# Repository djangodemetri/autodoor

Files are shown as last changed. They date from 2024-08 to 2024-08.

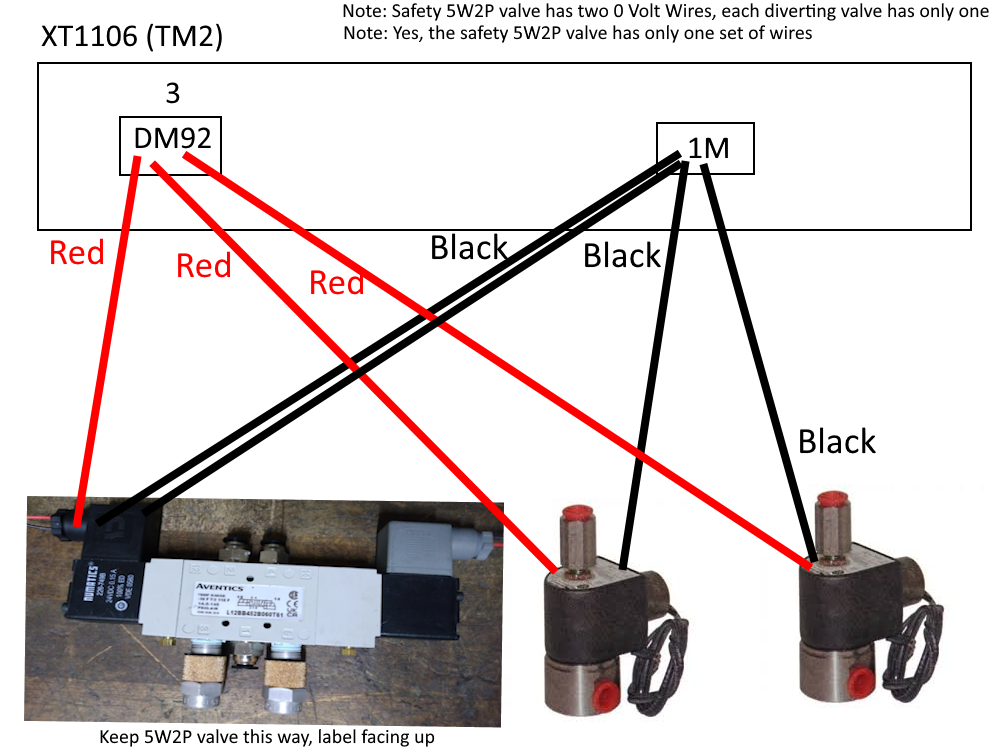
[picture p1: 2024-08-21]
Technician Diagrams/Safety 5W2P Valve_Diverting Valves Wiring Diagram.png

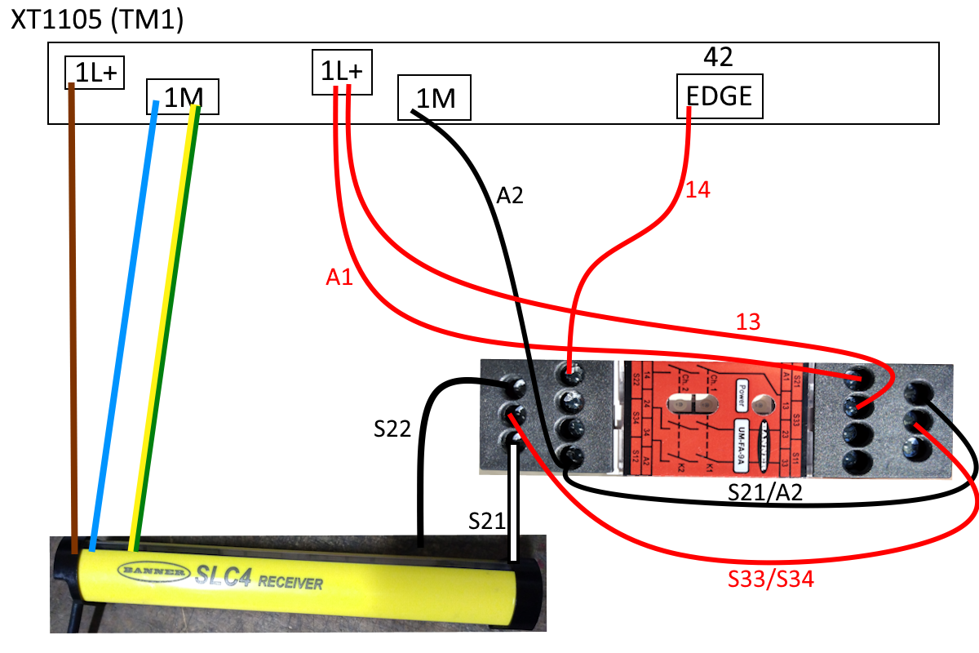
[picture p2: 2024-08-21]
Technician Diagrams/Light Curtain Receiver_Safety Relay Wiring Diagram.png

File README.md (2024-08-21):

White Industries is a machining company for billet aluminum bicycle components located in Petaluma CA. 
In order to meet growing demand, they hired me to create a pneumatic auto door that could be mounted to all of their machines (routers and lathes).
The company did not have any engineers as employees so I was the engineer and manager of the project.
In 2.5 months I designed, built, and tested a fully functional autodoor that meet all the necessary requirements:
1 Controlled by the host machine through ladder code
2 Scalable 
3 Safety (by using a Banner light curtain)
4 Documented so that the other employees could troubleshoot, maintain, and adapt the autodoor to other machines.
Please see the video demonstration for the final product.

It was abundantly fun and I am very thankful for the opportunity.

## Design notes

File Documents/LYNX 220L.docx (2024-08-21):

Continue:

Return switch valves

Return DIN connectors

Return Through beam

Return air cylinder brackets

Return M12 connector (wait) (Also determine color code before reutnring the M12 connectors

Call Bimba for adjusting air cushion

Emitter needs to have a U bracket that wraps around the back. The mounting plate is either above or below the plane of the emitter. Mount it to the two left screws only. We need to print washers. We need to find the distance of the emitter so the angle is okay, it might already be that 8cm but double check.

We need to find exact dimensions of the nose thread. Then we need to use the manual

We need to work in adjustability. For the air cylinder mounting we would want to drill slots instead of holes so that the air cylinder can be rotated if need be.
Make mounts relatively simple to machine, boxy

Interfacing:

The through beams must not open the door when it’s closed, aka, when DIC.M is triggered.

Through beam relay may not be necessary but it does isolate the sensors from a large power draw.

Why are there so many conditions for CLINT? Possibly it should be rewritten?

SSTA might be redundant because it’s included in the open door code? Or should it be in the close door code?
Maybe INRST should be wired to a button on the console, R17.6 which is the auto door button. If we want to be extra safe we could create another branch with CLINT and then a custom button/bit, but that wouldn’t work because it’s OR logic. We should replace INRST with R17.6 , because we can’t affect any other logic that may have INRST, but we have to make sure INRST did not provide any additional safety. *We don’t need to do this because KADOP will keep the door open and once CLINT is unlatched, the situation will return to normalcy.

Do we want the secondary solenoid to be wired normally open the door or normally close the door? If the power goes out nothing happens

Write OR condition for the secondary solenoid to be triggered, don’t purely rely on light curtain to trigger it

Think how software will interact with EDM. So the cycle is that the light curtain gets triggered, the safety relay is tripped, but because of the software, the XT1104 relay is held. With the EDM the light curtain may try to return to normal but it can’t because the reset circuit is being held open by the XT1104 relay, indirectly of course. The user hits the button and M53 executed, now the XT1104 input is off, the light curtain that is only held back by the reset circuit is now running again and everything returns to normal.

Be careful about adding DIC.M or DOC.M to reset code because this is what would define if the door could be closed before or after it has triggered DOC.M.

CLINT triggers DOP.R which then triggers KADOP, so once CLINT is off which should return to the normal state.

The operator closes the door by using M53 then the door is triggered. We need to make sure the machine does not start running the M program. It is probably safe to assume that DIC.M is already written and prevents the M program from running, considering they have just left DIC.M normally closed, implying that it would not run the code otherwise.

Problems:

ARST connects to INRST, what is ARST?

DOP.R/DOC.R have all the code written for them already. Does it make more sense to write both solenoids to DOP.R/DOC.R and have the switch valves run off the XT1104 input or does it make more sense to just connector DOP.R/DOC.R to the XT1104 input through the software? Let’s connect them through code. Figure out:

How does it reach return state?

Does this inhibit the system overall?

Delay implementing the force guided contacts. They are easy to retrofit and are not crucial quite yet. Plus it’s cheap so it’s easy to convince him later after the sting of the light curtain.

Does SDOC need to exist? By the time the door is ready to be closed, the primary code is now being executed. In fact, maybe it makes sense to not even allow the secondary solenoid to close the door.

ARST and INRST are controlled by the ALARM RESET EMG. RELEASE button

Grounding Forum (https://diysolarforum.com/threads/why-do-dc-systems-not-make-use-of-grounding-to-the-same-extent-as-with-ac.5152/)

dc Knowledge (https://electronics.stackexchange.com/questions/417172/why-do-engineers-usually-short-ground-and-negative-ports-on-a-dc-power-supply)

Wire neutral and earth together but only per unit, so we’ll have three separate wire bundles for the solenoid valves.

Is the normal output of the safety relay high? *Assume it’s high because it has and switches

Ground bolt is 7.5mm Looks like #10 (https://www.google.com/search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)

Code walkthrough:
1 Door closing, door not opening, light curtain triggered aka goes low, door not closed, ?

2 CLINT is latched because of ARST

3 DOP.R is latched by CLINT

4 *CLINT is opened by light curtain not triggered but DOP.R still on because KADOP/secondary system disabled because SDOP controlled completely by CLINT

5 *M53 is executed which turns off DOC.R on the open code and on close code and triggers DOC.R to close the door

Mounting:

Main solenoid: 27cm

Air cylinder: 66.35cm

Screw arrangement: 34cmx25cm

U brackets: 8/32in

5W2P brackets: M3

Diverting valve brackets: Probably SAE of M5

Installation Problems:

Switch valve does not function as intended

This depends on the switch valve, double check DIN connector fits and then order another

Return switch valves

Relay has slow return time (might not matter)

Second conveyor sensor did not come in d

One more relay for secondary solenoid (might not matter)

Adjust cushions

Potential Revisions:

Order equipment from a source other than McMaster, (likeG&G Hydraulics) to save cost. These companies have longer shipping time and less customer service but lower prices in lieu.
Likely the intake flow control valve and exhaust flow control valve are redundant. The exhaust flow control valve is more expensive so if metering is possible with only the intake flow control valve, likely $107 could be saved. If exhaust flow control valve is indeed skipped remember to buy mufflers for the main solenoids’ exhaust ports, 4 mufflers for 4 exhaust ports.

SMC’s sine air cylinder will naturally slow the cylinder the last couple inches or so due to its built in design. It’s as much as the 6258K154 (https://www.mcmaster.com/6258K154/) but has a 6-8 week lead time. Should be installed similarly to the 6258K154 but that has not been confirmed.

An air cylinder that has only cushions but not a magnet inside the cylinder for sensors to detect, (called sensor ready), is half the price; for example, 6475K216 (https://www.mcmaster.com/6475K216/) (double check specs before ordering). Mount a magnet on the extending end of the piston, (so the proximity sensor would be mounted at the position where the piston is fully extended).

If multiple machines will be fed from the same supply line then buy one regulator and supply line solenoid valve. Assuming the machines would be operable on the same pressure which should be reasonable unless one of the machine’s strokes is far longer than 24in.

Facts:

M52 open door

M53 close door

Supply pressure: 120psi

Outlet voltage:

232 data interface

0iD or 32iA

Door travel: 21 2/16 inch (53.657cm)

[

101533-00738

101533-00739

101533-01005

]

Door Height: APPROXIMATELY 44.5 inches

When one side is being pressurized, the other side will be evacuated

Serial Number: ML0022-006463

M02 is end of program code that might unlock the interlock

User Who Offered Help (https://www.practicalmachinist.com/forum/threads/robotics-automation-engineer.404319/)

Tips (https://automationforum.co/thumb-rules-and-tips-for-control-valves-selection-and-sizing/)

Adapters are 9/16

Exhausts are 11/16

Considerations:

We could use the code already in place or use external commands (M9-).

The door needs to be openable if the power goes out

For the manual air control valve it must depressurize more than the main control valve does.

https://www.machinetoolproducts.com/versabuilt-robotics-versadoor-pneumatic-cnc-door-opener-for-automation

*The door appears to not lock at all

*If the door is open, nothing else will happen because of that lock sensor

Might consider waiting to buy the safety beam until we see the door speed(a0)

The sensor only knows when the door is not closed. The operator will push the button to start the code.

M53 may already hop to next line of code. It may not know to wait because manually operated, it never needed to know

This auto door will clearly interface with the CNC, maybe it’s faster to just building the auto door and plug it in; don’t mount it and just watch the logic happen in real time. This rides on the assumption that we can easily make the adjustments. Maybe one exception would be depending if the safety relay will hold logic.

Does every piece have female or male threads?

For the 24inch stroke cylinder we could install more bump stops

References:

Midaco:

800 994 0146 Darrell

DN Solutions (Previously Doosan and Daewood):

888 dns 0010

973 618 2500

Fanuc US:

888 fanuc-us

Airflow Calculations:

At 60PSI the airflow is 8SCFM which (https://www.coastpneumatics.com/scfm-conversion/) is 1.62CFM at T=72 P=74.4PSIA PB=14.7PSI H=.85. The Cv is calculated to be .4 (https://www.swagelok.com/en/toolbox/cv-calculator).

General Parts:

Tubing

Piston Mounting Brackets Stationary

Piston

Piston Mounting Brackets Kinetic

Pressure Regulator

Solenoid

Control Valves Open (maybe needle valve?)

Control Valves Close (maybe needle valve?)

Piston lubricant

Release Value for safety stop

Main Solenoid:

4 to 2 solenoid

4xt33, 4ka92

How does it respond to logic?

Are the exhaust vents threaded? Yes because they say female outlets

Would cylinder speed depend on both pressure and depressure rate? This may be fixed if we have valves already, the valves needed to block the exhaust ports.

Consider flow rate: is 9 CFM enough?

https://www.grainger.com/product/ARO-Solenoid-Air-Control-Valve-2G621

Make sure it can operate at the PSI we are actually using

The supply will never be feeding both the solenoids at once so we only need to consider CFM for one solenoid.

Can we complete cut off solenoids if they’re only 4 way? *Because they get completely isolated thai shouldn’t be a problem. *So we shouldn’t need switch valves for the exhaust ports.

If 9CFM is too high, consider a lower CFM solenoid if cheaper?

https://www.amazon.com/ARO-Ingersoll-M212SS-024-D-G-2-Position-Solenoid/dp/B06XFMM7LT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

*200mA

Cheaper model with 50 min (https://www.zoro.com/aro-solenoid-air-control-valve-14-in-24vdc-a212sd-024-d/i/G2774816/?gclsrc=aw.ds)

7/6 Addendum:

Since the cushioning does not behave the expected way and we need to use exhaust ports we will likely need to control the speeds independently with 5/2 solenoid valve.

https://www.mcmaster.com/6425K14-6425K143/ This requires four less DIN(-$42), 4 exhaust control valves with muffler (+$24.16)[minus silencers], potentially both flow control valve. Would we want meter in only for flow valves?if we have to valves metering out then we might restrict the depressurize system too much. Difference in threads may need attention later, but because NPT male to NPTF female it may not deform those threads and it should be okay.

Tubing:

Fittings are usually push to connect

Make sure it can operate at the PSI we are actually using. It can, according to website linked right below.

Make sure the CFM is enough

Max SCFM at 60PSI is 3.5 (https://www.greenlinehose.com/content/Hose%20Flow%20&%20Sizing.pdf)SCFM

Mounting:

https://www.modularcomponents.com.au/building-blocks/

Angle Mount Information (https://cdn.automationdirect.com/static/specs/nitrad2hd2bore.pdf)

Angle Brackets for Air Cylinder (https://www.automationdirect.com/adc/shopping/catalog/pneumatic_components/pneumatic_air_cylinders/air_cylinder_accessories/d2am-1)

Pistons:

https://www.automationdirect.com/adc/shopping/catalog/pneumatic_components/pneumatic_air_cylinders/iso_15552/g40m500md-mc

https://www.hydraulicmegastore.com/product/32-550amak/

https://www.zoro.com/speedaire-air-cylinder-1-12-in-bore-22-in-stroke-nfpa-double-acting-5teg5/i/G7647272/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

https://www.mcmaster.com/6258K149/

Half of the price can be saved if we create a custom sensor setup or cushion setup. It’s possible to mount a magnet on the end of the piston, (where it mounts to the door), and then just have the proximity sensor at the middle point, (wherever the mount lies when the cylinder is fully retracted).

We have three states but only two inputs, but the normal force must equalize the piston force so you only need two inputs.

Calculator Cylinder Size (https://www.automationdirect.com/pneumatics/cylinders/cylinder_sizing)

Operation force is 15 pounds, 18.75 with 25% safety which is a minimum. We can assume there won’t be too much loss since the system doesn’t have that many components. MAKE SURE ROD DIAMETER MATCHES TABLE

RETRACTING FORCE WILL BE LESS

Air Cylinder Factors:

Bore

Pressure

Action

Damping

Safety

Airflow Calculations:

Assume maximum case.

Assume that pressure regulator is very close to the solenoid. Meaning the only piping where CFM becomes necessary is primary solenoid to cylinder.

Assume inner diameter of air housing is the same as the outer diameter.

Airflow Calculations (https://www.youtube.com/watch?v=Fbw3QlP2hTM)
Cylinder Dimensions:

Bore Diameter=29.633mm

Rod Diameter=7.874mm

Stroke=558.800mm

Pressure=60psi=.414MPa

Piping Dimensions:

Length=2000mm

Diameter=3.175mm

Airflow=2.435 cfm (23cfm from other calculator)

Sine cylinder has slowing effect naturally.

Seems like the REC cylinders are all legacy, why is that? (RECB25-550)

Is the slowing controlled by PLC or is it just mechanical?

Adjustable slowing?

If we order a cylinder without the reed switch does it still come with a magnetic inside?

Anything special about setting it up compared to other cylinders?

Returns?

Auto switch?

Force chart?

https://www.smcpneumatics.com/RECL25-550-C80C.html

Pneumatic Cylinder Sensor:

DOC.M is named “Auto Door Open Check Sensor.” NO sensor, when sensor is triggered then the NC DOC.M is triggered and the machine knows the door is already open.

Regulator:

Consider that the nominal pressure may differ, maybe buy a slightly higher PSI gauge

Make sure the pressure adjustment range has a range to and around 60PSI (Likely we would want to go lower than 60PSI, not necessarily higher so that sacrifice can be made if needed, but try not to)

Make sure CFM is enough

Filter

Bowl for condensation?

Light Curtain:

To back off the cylinder, it’s simple just triggering it backwards using the same system. Except when the power goes out this will not be viable for safety or just to open it. THIS WILL DEPEND ON WHAT SETUP THE AIR CYLINDERS WILL BE LIKE, maybe needle out system?

The door handle is going to trigger the light curtain unless we mount it at least 3.5 inches from the door’s edge.

Normal state is 24V, hazard detected is 0V (open door is 0V)

Does the signal stay low until the person’s hand is removed or is it on a timer?

Edge to handle: 4 inches

Edge to handle with arm: 6 inches

SEE CONSIDERATION(a0)

Door must wait until okay signal is given, (this likely could be the same as the normal close door and continue procedure). Check if there is a timer or if it’ll stay open indefinitely.

Fingers must be able to be unclamped?

How many pounds to open the door? Could an operator open it manually, in the case the power goes out?

Alternative: Have it closed with a button and require that someone is holding the button to close the door. This may eliminate the need for a safety beam

https://www.pepperl-fuchs.com/usa/en/classid_83.htm?view=productdetails&prodid=67155#datasheetcontent

If OSSD is used then a safety relay is needed as well. Make sure it is not a pulse signal model?

Consider a IP54 box (https://www.sick.com/media/docs/1/01/101/Operating_instructions_ReLy_OSSD1_en_IM0076101.PDF)

*It looks like the safety sensor only holds voltage when the object is obstructing the beams aka pulse.

We could remount the handle. Because it won’t be used much anymore it doesn’t matter if it’s in a weird or inconvenient spot.

https://www.wolfautomation.com/light-curtain-ultra-thin-thru-beam-160mm-det-1/

Does the light curtain run on AC or DC? DC
In safety, if the light curtain is exposed to coolant or water or any other substance inspect before using it again.

General Informaiton (https://info.bannerengineering.com/cs/groups/public/documents/literature/122452.pdf)

Trip or latch (Maybe buy a light curtain that does both and we can troubleshoot in the moment). Maybe just skip because safety relay may not be compatible.

Does the safety relay have enough power to operate the directional valves? Doesn’t matter if we use trip system.

https://www.bannerengineering.com/us/en/products/part.805795.html $642

https://www.bannerengineering.com/us/en/products/machine-safety/safety-modules/sr-im-series.html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

Through Beam Addendum:

https://www.wolfautomation.com/photoelectric-sensor-through-beam-pnp-45595/

https://www.balluff.com/en-us/products/BOS02AW

Throw dust into beam’s path to test if it still works

Says (https://www.automationdirect.com/adc/shopping/catalog/sensors_-z-_encoders/photoelectric_sensors/general_purpose_photoelectric_sensors/qmrhd-0p-0a)to use 24AWG, 100mA max which my calculations give 2.4W

Visible light may be susceptible to other light

Back to Light Curtain Addendum:

Is it possible to have the light curtain wire directly to the Lynx? It would have to compensate for the time difference between outputs to know when it’s a real trip. It would also need to input relays, which is not a bad thing considering there are plenty of spares.

Page 19 for Table of Terminals (https://media.distributordatasolutions.com/allenbradley/2017q1/74da9d8dcf82595eb507972877c303329b069640.pdf) Diagram (https://literature.rockwellautomation.com/idc/groups/literature/documents/at/safety-at065_-en-p.pdf)

EDM Explanation (https://blackcontrols.com/blog/f/external-device-monitoring)

Page 55 for Force Guided Upgrade (https://info.bannerengineering.com/cs/groups/public/documents/literature/179480.pdf) Possibly just across the safety system

Arc suppressors, see datasheet linked on page 60, Page 8 (https://info.bannerengineering.com/cs/groups/public/documents/literature/141249.pdf) suggests that we do not need arc suppressors because we are operating under 151V.

Prove the IM-T-9A can be used

Force Guided Relay (https://www.wolfautomation.com/relay-force-guided-3no-3nc-24vdc-led/)

With respect to choosing polarity for EDM reset circuit, it must be NC because the contacts are mechanically linked, so you can’t have 5 pin.

EDM protects against returning to normal state from safety state, but what if the contacts are welded in normal state and cannot be triggered to safety state?

1brown 2white 3blue 4black 5green

Directional Control Valve:

Do we need one that exhausts the air? Yes, because that is the third connection

Do we want spring return? Yes, it’s cheaper and should work just fine in this situation.

NC or NO? It appears we can set it up whichever way. The only possible problem is that hooking it up “backwards” must have airflow problems depending on how the solenoid is created.

There is a switch valve with speed control but it only has 1/4inch ports. Will there be enough adjustment to slow the air enough? Physically look at 1/4inch compared to 1/8inch, would the CFM change that (https://www.greenlinehose.com/content/Hose%20Flow%20&%20Sizing.pdf) much (https://www.engineeringtoolbox.com/air-discharge-hose-d_1523.html)? Will it actually save cost if we have to order different size hoses and connectors? Also is the speed electrically controlled? Don’t need it

Is 6ms fast enough? If so, no need for fast-switching. Don’t need it

https://www.automationdirect.com/adc/shopping/catalog/pneumatic_components/directional_control_solenoid_valves/solenoid_valves/avs-3111-24d

General Directional Valves (https://www.mcmaster.com/products/pneumatic-switches/single-action-electrically-operated-air-directional-control-valves-11/)

Predicted airflow is 3.36SCFM

*125mA

Revision:

https://www.emerson.com/en-us/catalog/automation-solutions/fluid-control-pneumatics/general-service-valves/asco-320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

https://store.flw.com/products/asco-series-8320-3-way-solenoid-valve-8320g174-24-dc.html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

Shuttle valve is a candidate but it works on pressure differential which mean we would need to have one of the solenoid operating at a higher pressure.

Use a 4 way 2 position valve with the exhaust valve sealed

Two 2 way valves that are wired in opposition

Different Spool Valves (https://www.sunhydraulics.com/sites/default/files/media_library/tech_resources/TT_US_PODirectional_Aug2015.pdf)

https://www.electricsolenoidvalves.com/1-4-3-way-24v-dc-electric-solenoid-valve/

https://us.misumi-ec.com/vona2/detail/221300030450/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

Probably L-Port type valve

For Parker manual (https://www.parker.com/content/dam/Parker-com/Literature/Fluid-Control-Division/Bulletins/PDFs/Parker-General-Cat-3-Way-Valves.pdf), page 17-B7

Search for “l-port” and “3 way selector”

Top choice for now (https://www.mcmaster.com/2565N15/)

B30

Alternative for the future (https://tameson.com/products/tp-db014b040f-024dc-solenoid-valve-3-2-way-1-4-inch-brass-fkm-0-2bar-24vdc)

Air-Exhaust Control Valve:

We might not need this at all, depending exactly on how the two solenoids interact

Supply Solenoid:

Use two relays, normally open in parallel with and logic to control the supply solenoid. The and logic is to have redundancy in the system. (Probably skip this, it doesn’t seem to add any more safety)

Make sure it can operate at the PSI we are actually using

Make sure CFM is good. With a Cv=1.4 the allowed airflow is 27 (https://www.swagelok.com/en/toolbox/cv-calculator)SCFM, should be good. But it shouldn’t matter because it’s been fed from the supply and has 1/4inch hosing so its airflow should be the least restrictive of all the components.

Should it be 220V or 24V? 220V limits the options.

Pressure assisted or zero pressure? Zero pressure to be safe
https://www.mcmaster.com/products/on%2Foff-valves/valve-type~solenoid/solenoid-on-off-valves-10/valve-starting-position~normally-closed/pipe-size~1-4/voltage~24v-dc/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

500mA

Flow Control Valves:

Mount as close to the air cylinder as possible for best results, (according to McMaster (https://www.mcmaster.com/products/flow-control-valves/inline-air-flow-control-valves/for-outlet-tube-od~1-8/))

https://www.mcmaster.com/62005k35/

Make sure CFM is good. 4SCFM at 73PSI seems sufficient considering the maximum airflow for hose is 3.5CFM. Should not be very restrictive at 60PSI.

Power Supply:

Does Lynx have power leads?

Must be able to supply:

Supply solenoid

Light curtain

Safety relay

Directional valves

Secondary solenoid

Odds and Ends:

1 to2 -> supply solenoid to primary/secondary solenoid

*Primary solenoid exhaust flow control valve (2 if 5 way solenoid)

*Secondary solenoid exhaust flow control valve (2 if 5 way solenoid)

Teflon tape for sealing connections

1/8inch pressure gauge (pressure regulator, also maybe for testing)

Push-to-connect adapters

Anti-rust spray for drilled holes (must not react with coolant)

Fuses, rated for 32V so we should be okay

2 Relays, through beam sensors, 24V, 100mA, 24AWG compatible

A 24V tester to activate relays (could go without but CNC has huge power draw)

DIN connectors? (https://www.amazon.com/43650-Solenoid-Prong-Connector-Indicator/dp/B09SHKJ7F3?sp_csd=d2lkZ2V0TmFtZT1zcF9hdGY)*Only 2 needed for main solenoid

Probably don’t need any ground equipment since we’re wiring everything through the Lynx

Wire sleeves

https://www.grainger.com/product/SCHNEIDER-ELECTRIC-Slim-Interface-Relay-6-A-Current-6LVJ8

End of Stroke Control:

Release valve controlled by proximity sensor

Progressive spring

Pulse air valve

Add extension to shorter stroke sine cylinder

Just have return stroke slower

Basic Ladder:

They are all push and hold by default

The second relay can be NC, which would be on. But if the relay before it is not on, then it doesn’t have any effect. Even if it is on

Think of toggling buttons as just paying attention to the rising edge

1 The PLC will record all inputs 2 The program will execute 3 the outputs are collected 4

When the tutorial said it was proper to use NO, the physical wiring is normally closed so that when it breaks it’ll open the circuit and turn the output off.

Scan Examples (https://accautomation.ca/understanding-the-plc-program-scan/)

If CLINT goes high then the door opens no matter what. In order for CLINT to go high:

AD Close Relay = 1

AD Open Relay = 0

Safety Sensor Edge On = 0

The door sensor must be out [DCLOSE is DIC.M is door lock sensor (out =0, in = 1)]

KEDGE = 1

Just delete KEDGE and replace it. Deleting KEDGE from CLINT (probably?) won’t affect anything else. Then you don’t have to worry about overwriting anything.

Strategy:

We were looking to buy an auto door option, what would we need to know about setting it up?

1 bill of materials

2 prototyping

3 Clear up details

4 testing

Routine:

Part is done and operator opens the door

User presses foot pedal to release clamp

User cleans part

User replaces part and presses pedal again

Closes the door

User presses button to start program

6/16:

Contact Doosan:
Questions;

Is it 0V that opens the door and 24V that closes it? Does it pulse or does it hold the voltage?

Does M52:

Stop the machine from running?

Does M52 know when the door is fully open?

It waits until the the auto door close/open button is pressed?

Is there a wait on input code?

Would Doosan send us the ladder code?

Considerations:

The sensor only knows when the door is not closed. The operator will push the button to start the code.

M53 may already hop to next line of code. It may not know to wait because manually operated, it never needed to know

If M00 or M01 is executed, then nothing will happen until Cycle Start is pressed.

M53 may already hop to next line of code. It may not know to wait because manually operated, it never needed to know

Cycle:

start:

The program ends. The door opens because of the M52 code.

Once the M52 code is triggered, the voltage on the relay changes, (but is it high or low?).

The machine must know somehow when the door is fully open. (it’s possible to just put this on a timer)

Then the door must wait for some signal from the operator, likely use a button on the console to close it.

Then the operator presses the continue button

The program runs

GOTO start

Interfacing the solenoid with the CNC relays:

The solenoid only accepts either 1 or 0, there’s no idle position.

1. We could only use 104.1 (M52) and once that goes high, then the door retracts. But we have no idea how it behaves in the software.

2. (This is all assuming the code runs either or, not pulse). We could place two relays after the internal relay, one NC and one NO. Then both relays would be in agreement and they would behave like one relay. Then connect them to the ignition terminal on the solenoid. *This would preserve the code’s behavior.

3. We could also use an entirely different single relay that would behave exactly as wanted but we would have to write some code for it, hopefully not much.

If we already have code written for M52 then we could just use M52 in the program.

Solenoid relay hooks into CB104.1 and CB104.2. (Because there are two separate relays that suggests a different logic scheme, one where we would need

Y01.1 is open door (maybe called FRDOP because he said it’s not the direct way). CB104.1 is the I/O name

Y01.2 is close door (maybe called FRDCL because he said it’s not the direct way). CB104.2 is the I/O name

Both M52 and M53 appear to be normally open. But if we fish through the code to see the direct connection we might find differing information

Consider cobot compatibility. But ultimately the cobot could just use a single binary signal as well, essentially the same as the CNC machine.

The hold logic is defined by ladder

Why are there two relays for it? Y1.1, hold until y1.2, unless maintenance and interlock are activated. The interlock requires a set time to elapse before M52 can be executed, which is dictated by ladder code.

Does the kit come with a sensor that tells us when the door is fully open or close?

Phone Call:

Maintanence Mode is M250

Keep relay holds whatever state it was, in case of power off

L000 is “0V”, I think he said it was for AC

Logic high is the M52 command

Address:

1325 Ross St # A, Petaluma, CA 94954

Dump:

Ladder system:

https://www.youtube.com/watch?v=OmqC7_2Ugd8

http://dermako.com/Fanuc_Web_Manuals/Prog/61863ev2.pdf

http://www.cncmanuals.com/fanuc/172/pmc-ladder-language-programming-manual/page/128

https://cdn.automationdirect.com/static/eBooks/PLC%20Handbook.pdf

Toggle Bit (https://www.youtube.com/watch?v=ig5QXp2Bb1s)

Kmap (keep in mind this kmap does not cover every scenario, it excludes the needed and gate)

LC | Auto | OpCl | Scenario: (1=door open || 0=door close)
0 | 1 | 0 | X
0 | 1 | 1 | X
0 | 0 | 0 | 0
0 | 0 | 1 | 1
1 | 1 | 0 | 1
1 | 1 | 1 | 1
1 | 0 | 0 | 1
1 | 0 | 1 | 1

Relay Chain:

Normal function:

Connect internal relay leads to solenoid leads. *When close door, logic high. *When open door, logic low.

Lever:

3 or 4 position

Two NO, one NC

Maintain

Logic to Relays (http://www.relaiscomputer.nl/index.php/elements)

3 Position NC NO (https://cdn.automationdirect.com/static/specs/cents22mmselect.pdf) (https://www.automationdirect.com/adc/search/search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)

Is the safety supplied?

1 Allow the door to operate normally (aka standby)

2 Open the door

3 Close the door

4 Override the primary solenoid

We could have two release valves on when secondary is triggered, which would get rid of any primary influence.

Idle:
Step 1:

a) Trigger both release valves, making primary solenoid completely ineffective no matter which state it is in
b) Activate control relay for secondary solenoid

Step 2:

Secondary Control (Safety):

Return time would be covered because the code will not proceed until the door is fully closed.

Primary is pressurizing left, venting right. Secondary in pressurizing right, venting left. They must have valves because if they’re trying to do opposite actions, then both sides of the cylinder will be vented. The valves should then render one solenoid ineffective.

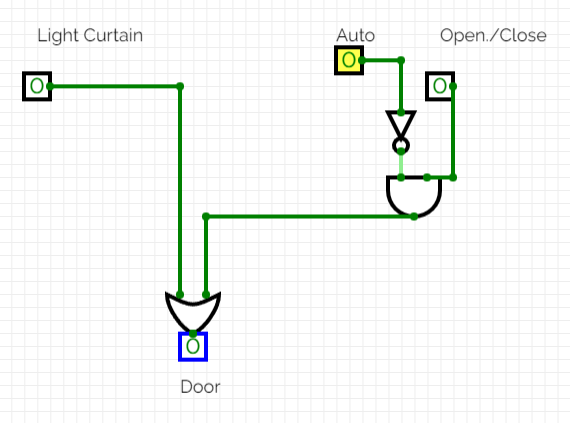
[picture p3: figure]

Caption: If you’re looking at this in the future, I believe the logic is reversed. That is, 0 is open and 1 is close.

4952K721

Do More Designer: vmlcvrgulkerpkbrim@bbitf.com

Temporary:

Primary Solenoid Considerations:

Do we need door close relay? DOC.R

Secondary Solenoid Considerations:
Safety relay is pulse so:

1 Add a few simple lines of code

2 Redo system (This will likely just be Option 1 weirdly)

Let’s go with 1

1 We need code for directional valves

2 We need code for secondary solenoid

So the safety relay goes high temporarily. It will send that pulse to (EDGE.M or KEDGE). The code will run as intended for everything else. Meanwhile:

1 EDGE will trigger Y37.7 which will activate the directional valves. It will need to be toggle code that is turned off likely when DOP.R is.

2 EDGE will trigger Y37.8 which will activate the secondary solenoid. It will need to be toggle code that is turned off likely when DOP.R is.

Because we are able to program toggle bits our system should work.

Software has what we need, even safety and cobot code
The system we made does not directly work with the code but we can easily adapt it. I will need to add a couple lines of code but they don’t change existing code at all. We will back up the data and I have low risk ways of testing the code.

I know how the code roughly will work but not exactly. It makes more sense to figure that side out when we actually have the door built.
So now I’m generating the bill of materials.

Choose which air cylinder

Light curtain placement, remounting the handle?

Trip or latch, meaning bypass software or don’t
Do you want every connection to have push-to-connect?

For less important components would you like to buy them from Amazon or something like that?

Do we want to power the solenoids and light curtain on the Lynx or have a dedicated power supply? Do we know if the Lynx has 24V power source?

Adjustments: 1.5inch air cylinder

Two (or more) safety beams connected in parallel with relays

Airflow Calculations 1/8inch:

1/8in pipe has a maximum airflow of 3.5SCFM. The airflow of the cylinder is _.

Start with finding the airflow of the air cylinder in SCFM and CFM. Use the equation and cross reference it to the table that was given. Once that number is found then it’s a matter of finding pieces that correspond.
Set up assumptions first
A=.110SCFM which makes sense because the total volume of air per minute is only .027CF. We are using a small cylinder, with not many cycles so it makes sense it would be a number pretty close to the volume.

The maximum flow of a 1/8inch hose at around 60PSI is 3.5SCFM which is .88CFM (assuming T=72 P=59.7 B=14.7 H=.84). The calculated airflow for the air cylinder is .1104SCFM, using same parameters listed before.

Cv calculated (https://www.swagelok.com/en/toolbox/cv-calculator) with PI=59.7 P2=54.7 AF=3.5SCFM T=72 SG=1, Cv=.218. All pieces need at least 3.5SCFM or Cv=.218.

Resolution needs to be an inch. Let’s say we have 4in of protection, we need 5 receivers. The receivers normally normally on so that when one faults/power goes out, the door automatically opens. If we connect all 5 in parallel, then it becomes a 5 input and gate. To work with this we could:

1 Wire the sensors in series so that the voltages add up, but that would mean voltage regulation which would be somewhat complicated.

2 Wire the sensors normally off and when one is triggered it gives the 24V for the relay to switch on. This is not particularly safe because if we get an open circuit, (either naturally or from a fuse blowing), the door will continue to operate normally. We could use a relay to reverse the logic. But if one of the sensor fails, (unless short circuit), then the system would have no way of knowing and would continue indifferently.

3 Use 5 different relays all wired correctly. If power cuts out or there is an open circuit, the door automatically opens.

So we make a redundant receiver for each of the “main” receivers, (exception of one), which would cost $300 for the whole setup.

Piston definitely creates too much force to be innocuous

Returns:

3 way 2 position valve from Grainger: branch 742 (5760 commerce boulevard, rohnert park ca 94928)

13 and 14 is an unpowered relay. The CNC relays can either be powered or unpowered.

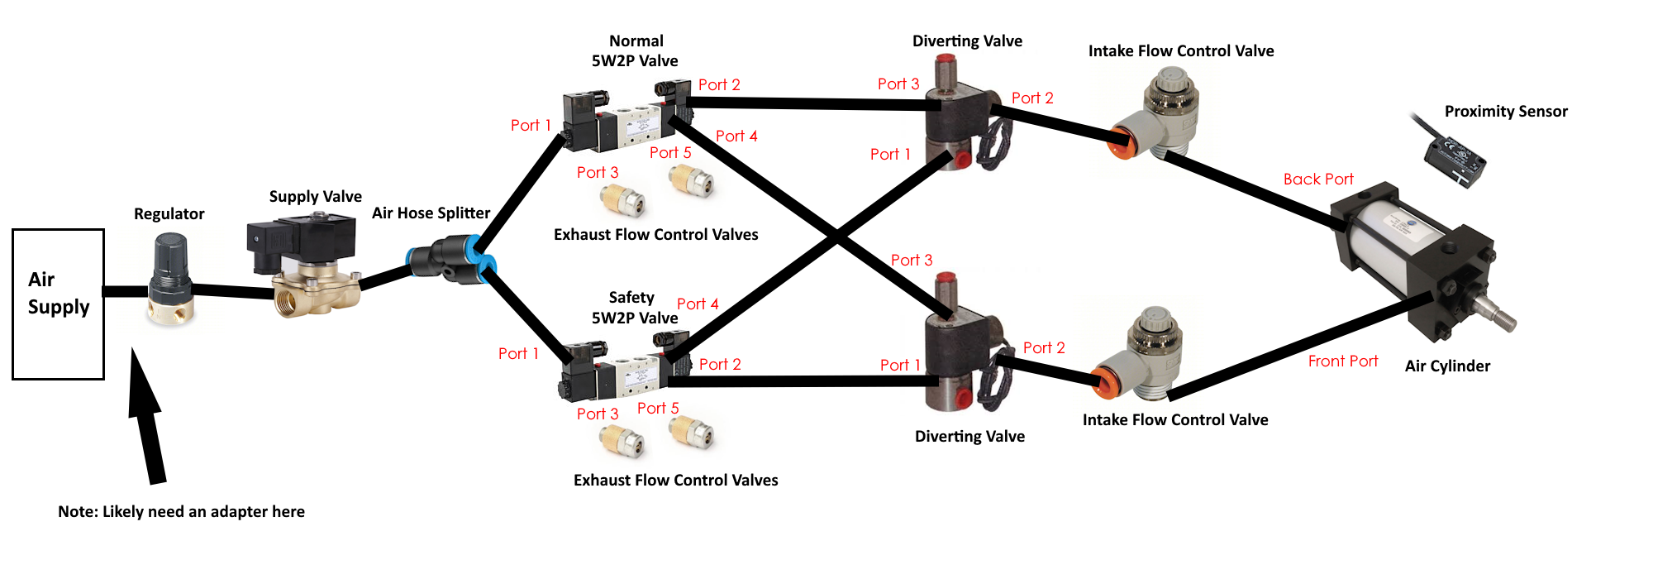
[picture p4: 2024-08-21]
Technician Diagrams/Pneumatic System Layout Picture (Figure _).png

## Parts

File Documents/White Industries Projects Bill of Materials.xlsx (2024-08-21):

Auto Door Project: |  |  |  |  |  |  | Additional Information:
Product | Quantity | Price | Notes | Backup | Company | Order Numbers
Air Cylinder (https://www.mcmaster.com/6258K154/) | 1 | 444.74 |  | 20 inch alternative (https://www.mcmaster.com/6258K144/) | McMaster | In Alec's email | Account email: alec@whiteind.com
Supply Valve (On/Off Valve) (https://www.mcmaster.com/4711K512/) | 1 | 123.78 |  |  |  |  | Account Password: fhAG65!@bm42hk (This may have been changed by Doug)
5 Way 2 Position Valve (5W2P) (https://www.mcmaster.com/6425K14/) | 2 | 347.34
Exhaust Flow Control Valve (Speed Valve) (https://www.mcmaster.com/9164K12/) | 4 | 107.64
Diverting Valve (Switch Valve) (https://www.mcmaster.com/2565N15/) | 2 | 334.48 |  |  | Grainger | #WEB2442639857
Pressure Regulator (https://www.grainger.com/product/WILKERSON-Compressed-Air-Regulator-Brass-6B216) | 1 | 27.49
Intake Flow Control Valve (Speed Valve) (https://www.grainger.com/product/SMC-Speed-Control-Valve-NPT-x-4DGR3) | 2 | 30.10
Proximity Sensor (https://www.automationdirect.com/adc/shopping/catalog/sensors_-z-_encoders/magnetic_proximity_sensors/rectangular/mdr-ap-1a) | 1 | 49.00 |  |  | Automation Direct | 13046639
Air Hose (https://www.automationdirect.com/adc/shopping/catalog/pneumatic_components/flexible_pneumatic_tubing_-a-_hoses/straight_flexible_tubing/pu14blk100) | 1 pack of 100ft | 31.00
Push to Connect Splitter (https://www.automationdirect.com/adc/shopping/catalog/pneumatic_components/push-to-connect_pneumatic_fittings/union_y/uy14) | 1 pack of 5 | 15.50
Teflon Tape (https://www.amazon.com/D-NYX-Rolls-Extra-Teflon-Inches/dp/B0BZWYCV6D) | 1 pack of 5 | 3.99 |  | Thread Sealer (https://www.amazon.com/Permatex-80632-Thread-Sealant-PTFE/dp/B000HBNTGY) | Amazon | In Alec's email
Regulator Gauge (https://www.amazon.com/Best-Pressure-Gauge-Center-Mount/dp/B01BZF40RC) | 1 | 6.99
Push to Connect Adapters (https://www.amazon.com/TAILONZ-PNEUMATIC-Straight-PC-1-4-N2/dp/B08F4YHR1V?sp_csd=d2lkZ2V0TmFtZT1zcF9hdGY) | 1 pack of 20 | 18.99
Electrical Wire (https://www.amazon.com/Silicone-Electrical-Colors-Stranded-Flexible/dp/B08F7CWMRX?s=industrial) | 2 pack of 30ft | 15.96
Fuse Holders (https://www.amazon.com/Inline-VANTRONIK-Waterproof-Standard-standard/dp/B081YDV8PS) | 1 pack of 6 | 7.59
2 Amp Fuses (https://www.amazon.com/Standard-Blade-Fuse-Automotive-Truck/dp/B08MYFLTZP) | 1 pack of 20 | 4.99
Butt Connectors (26-24 AWG White) (https://www.amazon.com/Shrink-Solder-Sleeve-Crimpless-Connectors/dp/B00IEFOD10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) | 1 pack of 10 | 7.25
Heat Shrinks
Light Curtain (https://www.bannerengineering.com/us/en/products/part.805795.html) | 1 | 490.00 |  |  | DigiKey | 82409662
Single Ended Cordset (M Connector Type) (https://www.bannerengineering.com/us/en/products/part.70880.html) | 2 | 66.00 | Not necessary (mouse over to see comment)
Safety Relay (https://info.bannerengineering.com/cs/groups/public/documents/literature/141249.pdf) | 1 | 272.00 |  |  | Steven Engineering | Purchase Number: 1 / 77C5AA6AF493578C16DD5BF2EB6C56181532 / 7021521
(Section for hardware for the future)
Final Total (before taxes and shipping) |  | 2404.83
Conveyor Sensor Project:
Product | Quantity | Price | Notes |  |  | Order Number
Proximity Sensor (https://www.automationdirect.com/adc/shopping/catalog/sensors_-z-_encoders/photoelectric_sensors/general_purpose_photoelectric_sensors/cxp-ap-1a) | 2 | 132.00 |  |  |  | Ref # 13052712
Ring Terminals (https://www.amazon.com/26-24-Heat-Shrink-Ring-Terminal-Stud/dp/B01MYGZNJY?pid=faX70fC&s=industrial) | 1 pack of 10 | 8.18 |  |  |  | In Alec's email
Reflector (https://www.automationdirect.com/adc/shopping/catalog/sensors_-z-_encoders/photoelectric_sensors/reflectors_and_lens_adapters/rl106g-1) | 2 | 9.50 |  |  |  | Ref # 13052712
Light Bar Project:
Product | Shortcut Link | Quote | Notes
A63L-0001-0988#RLGS | Fanuc Login (https://login.fanucamerica.com/oamfed/idp/samlv20) | Quote (https://docs.google.com/document/d/1T-p4G3XC9pq5fUbXCRdvvnkKDPJJkoN5rQzf2kjM_08/edit) | Needs to be purchased
A63L-0001-0986#25R02N-J |  |  | Needs to be purchased

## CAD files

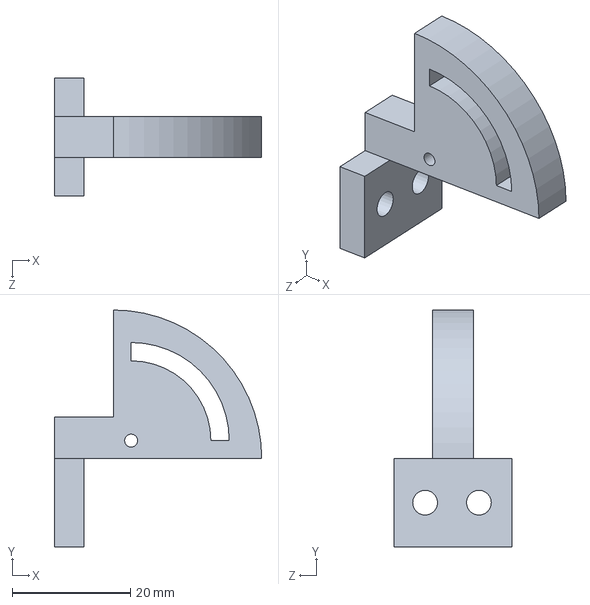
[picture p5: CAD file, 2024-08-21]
3D Printer Files (Solidworks)/Light Curtain Receiver (Bottom) Bracket Resized.SLDPRT
35.1 x 40.1 x 20.0 mm

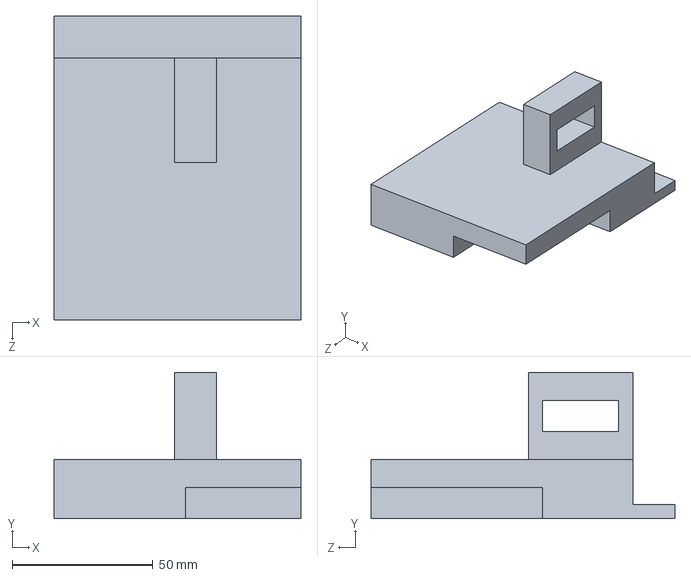
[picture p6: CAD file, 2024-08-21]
3D Printer Files (Solidworks)/Air Cylinder Nose Bracket.SLDPRT
87.7 x 51.9 x 108.0 mm

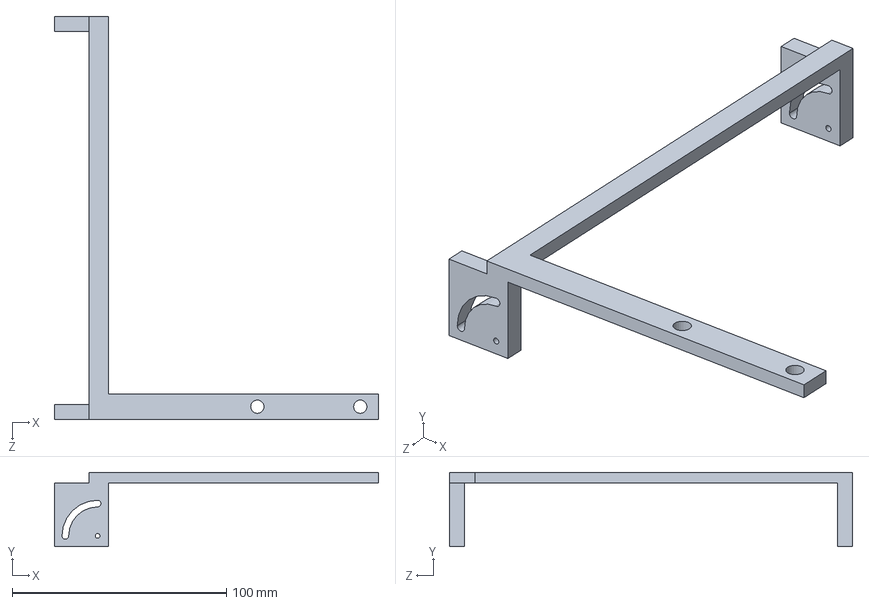
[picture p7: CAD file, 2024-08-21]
3D Printer Files (Solidworks)/Light Curtain Emitter (Top) Bracket.SLDPRT
151.1 x 34.6 x 188.0 mm

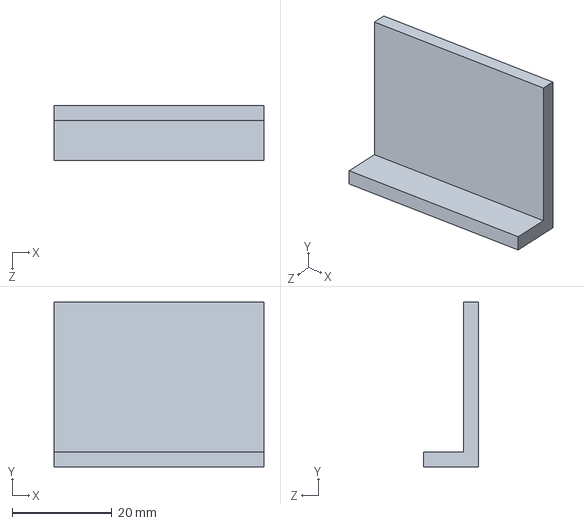
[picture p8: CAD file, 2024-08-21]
3D Printer Files (Solidworks)/Conveyor Belt Retroreflector Bracket.SLDPRT
42.0 x 33.0 x 11.0 mm

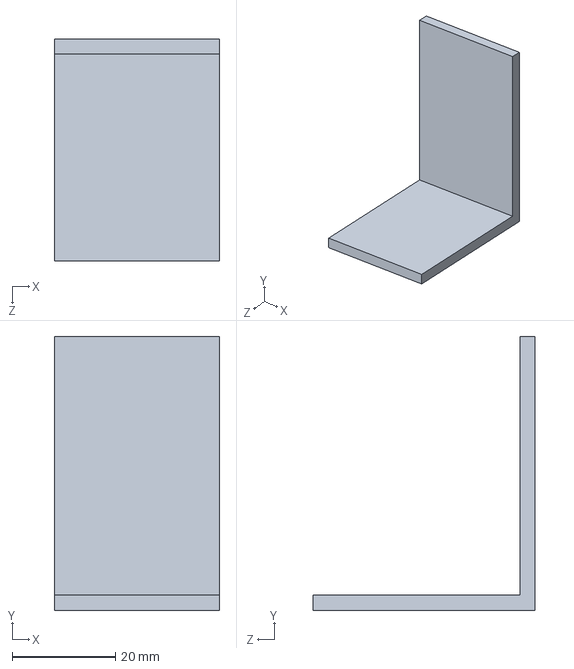
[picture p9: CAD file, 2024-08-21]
3D Printer Files (Solidworks)/Conveyor Belt Sensor Bracket.SLDPRT
32.0 x 53.0 x 43.0 mm

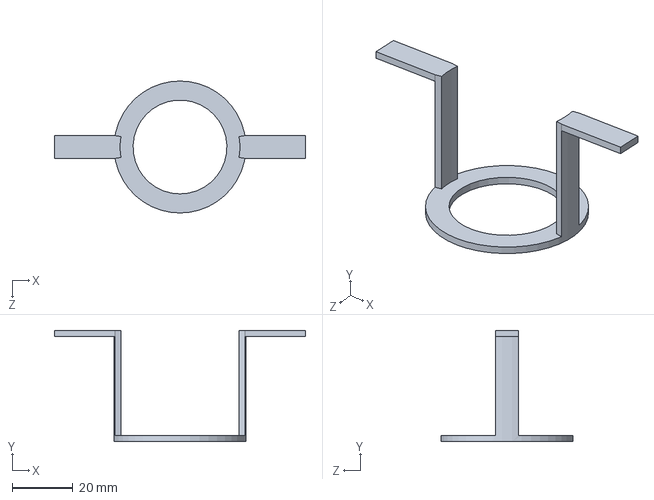
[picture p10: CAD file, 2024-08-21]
3D Printer Files (Solidworks)/Pressure Regulator Bracket.SLDPRT
82.9 x 36.7 x 43.6 mm

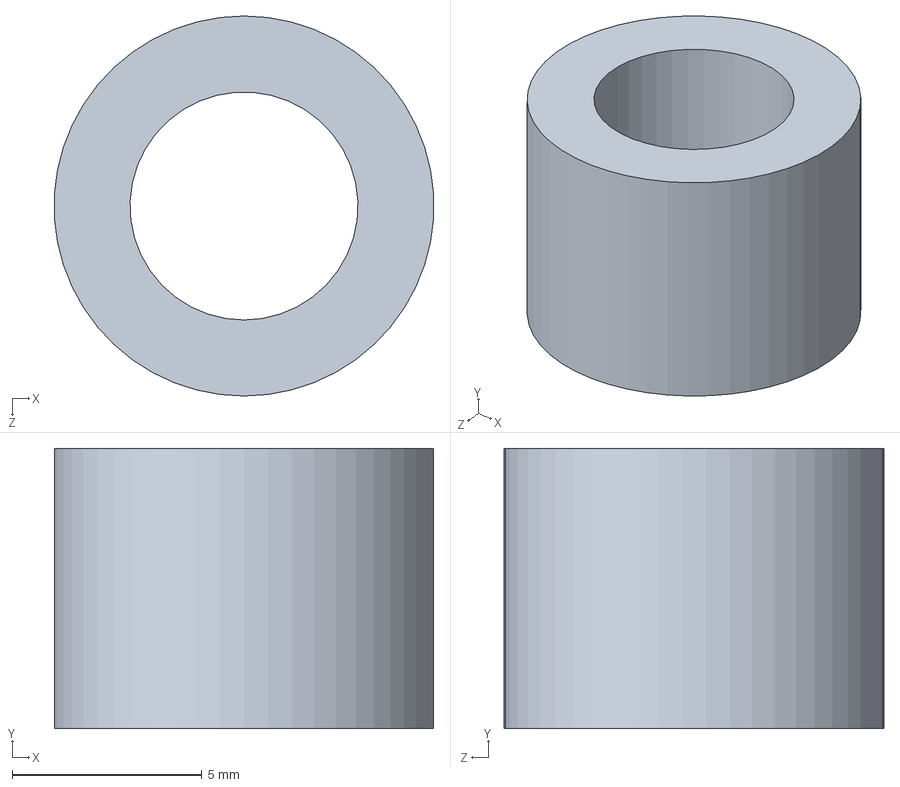
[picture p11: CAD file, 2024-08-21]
3D Printer Files (Solidworks)/Light Curtain Emitter (Top) Bracket Washer.SLDPRT
9.98 x 7.38 x 10.0 mm

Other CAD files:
3D Printer Files (Solidworks)/Light Curtain Receiver (Bottom) Bracket Resized 3mf.3MF
3D Printer Files (Solidworks)/Light Curtain Emitter (Top) Bracket Washer 3mf.3MF

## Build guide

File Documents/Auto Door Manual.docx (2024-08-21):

Table of Contents:

Introduction:

Safety - Page 1

Basic Operation - Page 1

How to Operate Auto Door - Page

Mechanical:

Specifications - Page

Mechanical Parts - Page

Adjust Door Speed - Page

Maintenance - Page

Electrical:

Electrical Parts - Page

What Relays Used - Page

Coding:

How to Read the Code - Page

Troubleshooting:

Try the Quick System Check First - Page
Door Does Not Open - Page

Door Does Not Close - Page

Light Curtain Does Not Open Door - Page

Door Time Out Alarm Message - Page

Quick System Check:

Quick System Check Procedure - Page

Introduction:

Safety:

a) Refer to the official Fanuc maintenance manual for thorough description on safe practices.
b) When modifying the electrical connections in the back of the machine, be sure to unplug the machine from every source of power, (in this case likely just the outlet), and wait the recommended time for the inductors and capacitors to discharge. This time is likely given in the maintenance manual.
c) If circuitry is exposed, pay special attention to the employees around you. If they bump you or touch circuitry serious injuries may occur.
d) Do not use super cheap ($20) multimeters ever. They do not have the proper safety circuitry; if they experience overvoltage/overcurrent they may ignite.
e) When disconnecting pneumatic components, make sure to shut off connection to the air supply.
f) The light curtain has green LEDs. If these are off do not operate the machine. Just because these LEDs are on does not mean the safety system is functioning.

Basic Operation:

Please see Figure _ for aid.

The air cylinder is moved when one side is pressurized and the other is depressurized. This means you need a device that can control how much air travels between the two sides. This device is called a 5 way 2 position valve.

There are two in this system: normal and safety. They are the same model and behave almost exactly the same. They are controlled by M-code, specifically M52 (the code to open the door) and M53 (the code to close the door).

The system must be able to switch from the normal 5W2P valve to the safety 5W2P when a dangerous situation occurs. This is achieved using diverting valves, (sometimes referred to as switch valves because they switch between the normal and safety 5W2P valves). Referring to the diagram it can be seen that both 5W2P valves run through them. When a dangerous situation occurs the CNC will trigger a relay that activates the diverting valves, cutting off the normal 5W2P valve’s ability to control the air cylinder; at this point, only the safety 5W2P valve can control the air cylinder. Once the danger has passed, the diverting valves will switch back, cutting off the safety 5W2P valve and allowing only the normal 5W2P valve to control the air cylinder.

But how does the CNC know when there’s danger? Mounted in front of the door is a light curtain which is a set of lasers that, when they get blocked, a relay inside the CNC is triggered. The software then sees this triggered relay and triggers another relay to engage the safety system, (safety 5W2P valve and diverting valves).

Keep in mind there are two sensors that tell the CNC when the door is fully opened or fully closed.

How to Operate Auto Door:

a) Open the door.

Place M52 in the M-code

b) Close the door.

Place M53 in the M-code.

c) Reset the door after the safety system has been triggered

Press the ALARM RESET EMG. RELEASE button on the keyboard. Then door should operate normally.

Mechanical:

Specifications:

The system runs on __ PSI.

Every electrical piece is on 24VDC.

All neutral and earth terminals are grounded.

24 AWG wire is used for all connections

Components:

Air Cylinder:

Purpose: To open and close the door

Basic Information: This air cylinder is “sensor ready,” meaning it has a magnet attached to the back of the piston, (remembering the piston is internal, sitting in the sleeve). This magnet triggers the magnetic proximity sensor talked about in the section Electrical Parts.

The air cylinder has adjustable air cushions that stops the piston from slamming into the sides of the sleeve walls.

Operation: The air cylinder has two chambers separated by the back end of the piston. To extend the piston, send air into the black chamber and evacuate air from the front chamber. To retract the air cylinder, send air into the front chamber and evacuate air from the back chamber.

Air to which side? | Direction of piston
Back | Extends
Front | Retracts

5 Way 2 Position Valve (5W2P):

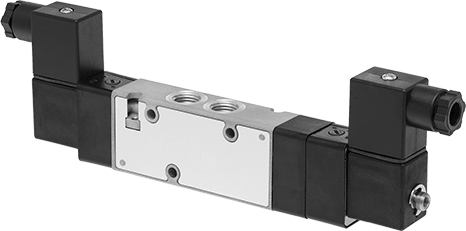
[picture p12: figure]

Purpose: To send and evacuate air to either chamber of the air cylinder. This is the main component of the auto door.

Basic Information: “5 way” means there are 5 ports: 1 supply inlet, 2 outlets (to air cylinder), 2 exhaust ports (metered with exhaust flow control valve). “2 position” means it is always pressurizing and evacuating, (there is no mode where no air flows).

There are two solenoids because this is a double action valve. Once a solenoid is initially powered, the valve will maintain its position even after the solenoid has lost power.

This particular part actually has NPTF threads. If that means nothing to you, then ignore this.

Operation: In order to understand its operation consult Figure _. Both diagrams feature the 5W2P valve and an air cylinder. The 5W2P valve seems to have two parts, both with repeating 1,2,3,4 and 5. These two sections do not represent the valve mechanically, they only represent the two positions the valve can be in. So this valve only has 5 ports, not 10. You can see there are two different positions by seeing how the air cylinder’s air lines switch.

The diagram on the left will be called Position 1. In Position 1, air flows in two directions.
Direction 1: From the supply (1) to the first outlet (2).

Direction 2: From the second outlet (4) to the second exhaust (5).
Because air is flowing into the left chamber of the air cylinder and out the right side of the chamber, the piston moves to the right.

The diagram on the right will be called Position 2. The idea is the same and now the piston moves to the left. These two positions are why it is called “2 Position.”

Please note that the T next to 3 in Position 1 and the T next to 5 in Position 2 means the air flow is blocked entirely.

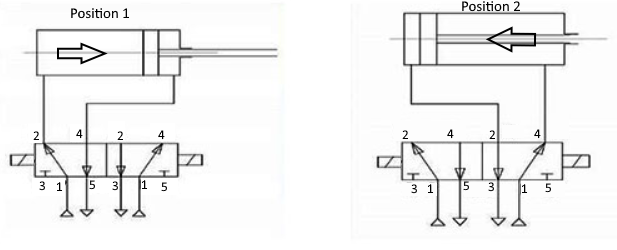
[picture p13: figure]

There are two solenoids in the 5W2P valve, (called double action 5W2P valves). Applying 24VDC across the terminals shown in Figure _ activates the solenoid.

Power to which solenoid, (label facing viewer) | Door open or close? | Piston movement | Port that sends air to cylinder | Port that pulls air from cylinder | Port that exhausts
Left | Open | Extend | 2 | 4 | 5
Right | Close | Retract | 4 | 2 | 3

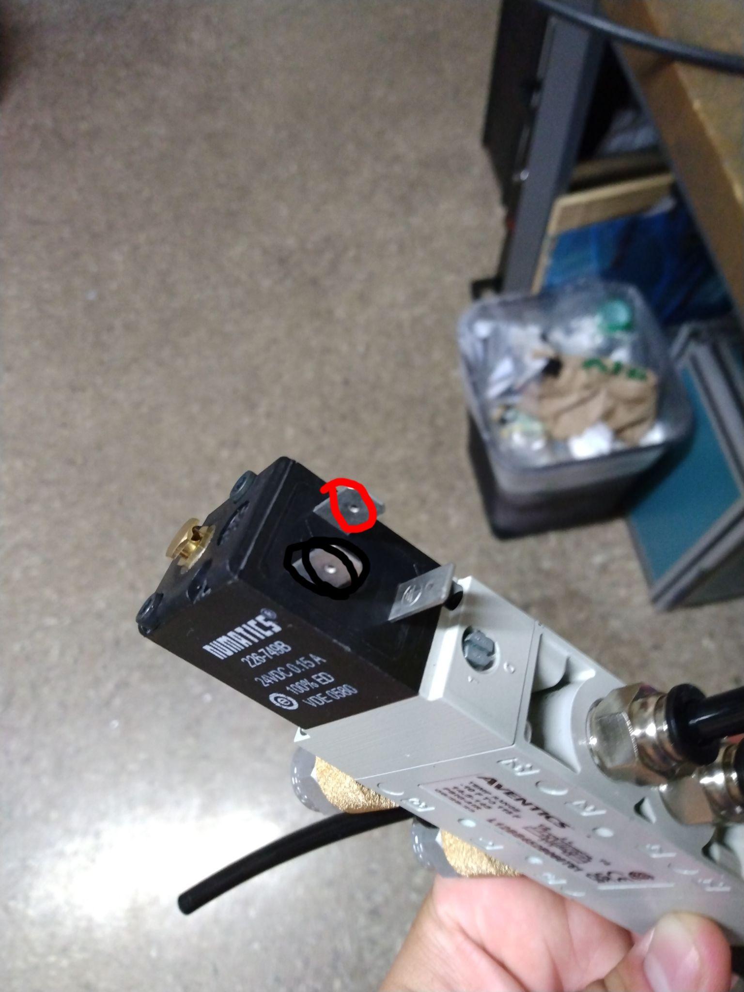
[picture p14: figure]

Figure _:

Diverting Valves (Switch Valves):

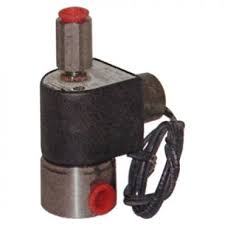
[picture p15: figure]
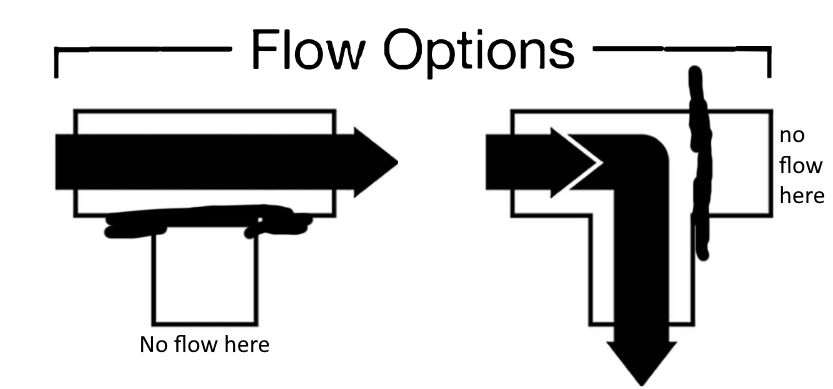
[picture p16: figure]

Purpose: In this system, two 5W2P valves are connected to the air cylinder: normal 5W2P valve and safety 5W2P valve. The two diverting valves allow the machine to switch between these two 5W2P valves. When one 5W2P is allowed, the other is completely blocked off.

Basic Information: Don’t put fingers inside, I dunno?

Operation: A diverting valve has three ports, called Port 1, 2, and 3. When the solenoid is unpowered it allows flow between two ports, (in practice Port 2 and Port 3). When powered, it blocks Port 3 and allows airflow only between Port 2 and Port 1. This table summarizes the actual flow pattern for the valves used.

They are controlled by the same terminal that controls the safety 5W2P valve, meaning both diverting valves and the safety 5W2P valve turn on and off at the same time.

Power to solenoid? | Allows | Blocks
No | Port 2 and Port 3 | Port 1
Yes | Port 2 and Port 1 | Port 3

Supply Valve:

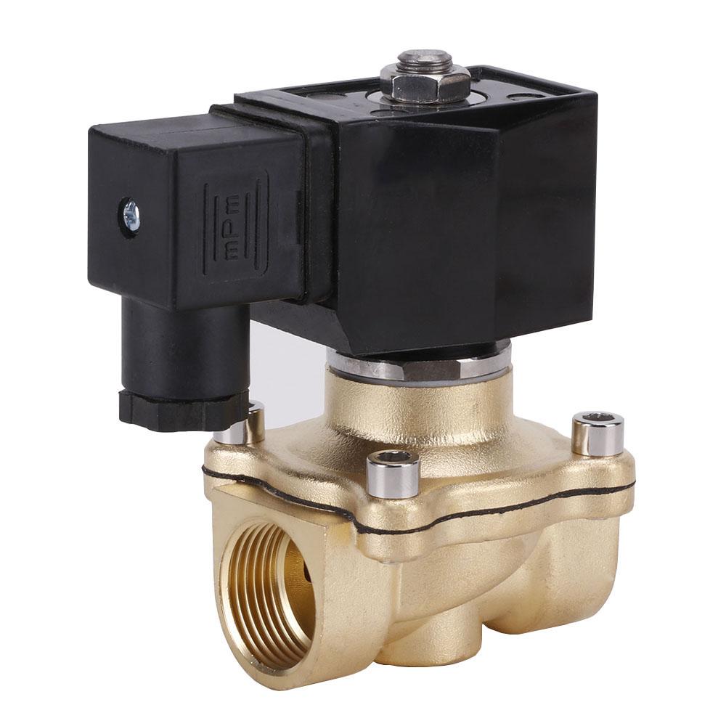
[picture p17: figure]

Purpose: The purpose is to cut air to the entire system in case of a power outage. This is very important because even though the power cuts out, the excess still in the line does not and the air cylinder can continue to move uncontrollably.

Basic Information: The supply valve is an on/off valve. It is a normally closed valve.

Operation: No power = no airflow.

Powered? | Airflow?
No | No flow
Yes | Flow

Pressure Regulator:

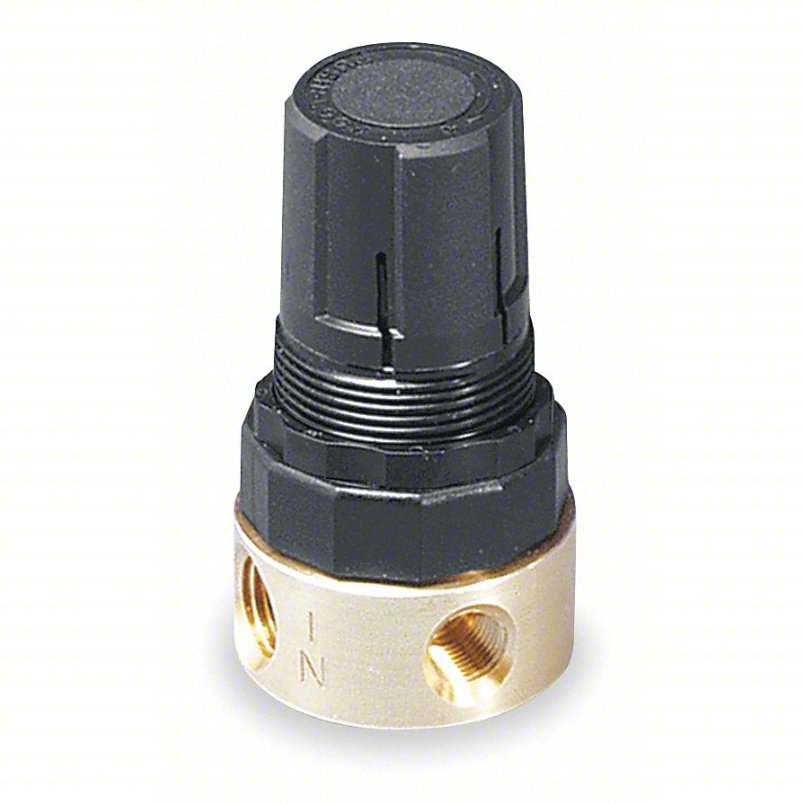
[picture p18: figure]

Purpose: Change the air pressure dummy

Basic Information: None

Operation: To adjust the pressure pull up on the black knob and twist. To lock the knob, push down.

Exhaust Flow Control Valve:

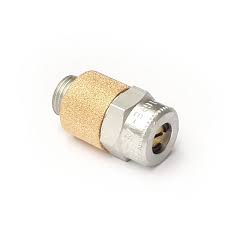
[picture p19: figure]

Purpose: The exhaust flow control valve controls the speed of the air cylinder by controlling the amount of air emitted from the 5W2P valves.

Basic Information: Bolt size is 11/16.

Operation: They can be adjusted with a small flathead screwdriver. Keep in mind this is one of two flow control valves that dictate the air cylinder’s speed.

Rotation | Speed up or slow down?
Clockwise | Speed up
Counter clockwise | Slow down

Intake Flow Control Valve:

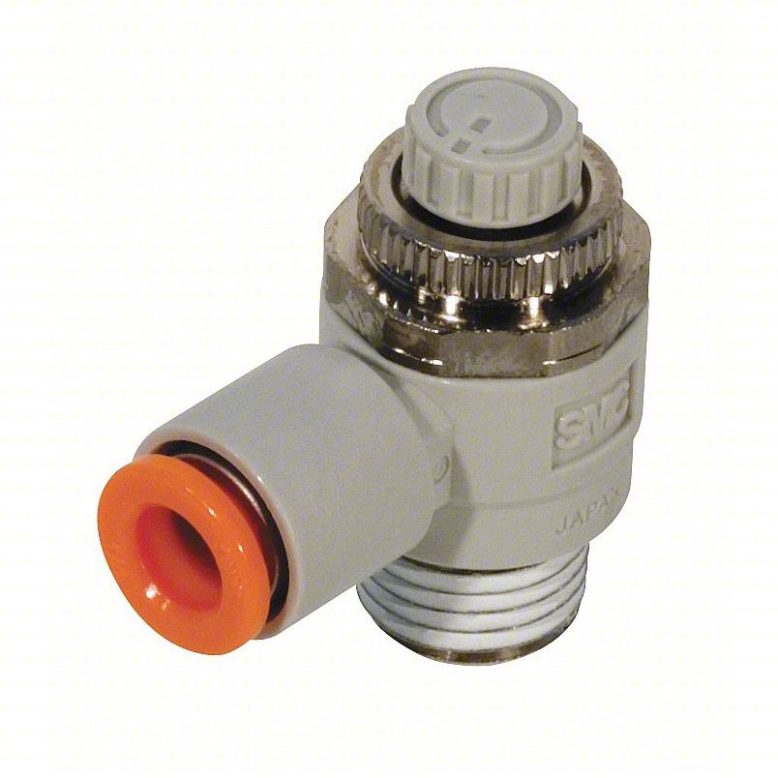
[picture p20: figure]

Purpose: The intake flow control valves control the speed of the air cylinder by controlling the amount of air that enters the air cylinder.

Basic Information: Inlet position can be adjusted independent of tightening/loosening the threads.

Operation: The adjustment is the white circle on the top.

Rotation | Speed up or slow down?
Clockwise
Counter clockwise

Magnetic Proximity Sensor:

Purpose: To “tell” the machine when the door is fully open, (when the piston is fully extended), by sending 24V to a relay in the back of the machine.

Basic Information: A proximity sensor is an electronic device that can “tell” other machines when a desired object is close to the proximity sensor. In this case, the proximity sensor detects magnets. The overall purpose of the magnetic proximity sensor in this system is to “tell” the machine when the door has is fully open, (when the piston is fully extended).

The magnetic proximity sensor has an orange LED that lights up when a magnet is detected.

Operation: The air cylinder has a magnet attached to the back of the piston, (inside the casing so the magnet is not visible from the outside). The magnetic proximity sensor is to be attached to on the air cylinder, positioned next to where the magnet will be when the piston is fully extended.

The magnetic proximity sensor has one side that is sensitive to magnets. If this side is not mounted near the air cylinder the magnetic proximity sensor may not be able to detect the piston magnet. (I can’t remember exactly what side it is but I believe it is the largest side that has no markings on it).

The detection range is very small so the magnetic proximity sensor must be very close to the air cylinder casing.

The magnetic proximity sensor has three wires: brown, black, and blue. Brown is the 24 Volt Wire. Blue is the 0 Volt Wire. The black wire is the output to signal to the machine when the magnetic proximity sensor detects the air cylinder’s magnet. It works like this: when the magnetic proximity sensor does not detect the air cylinder’s magnet, the black wire will produce 0V. When it does detect the air cylinder’s magnet, (aka when the door is fully open), the black wire will produce 24V.

Light Curtain and Safety Relay:

Purpose: To open the door if an object is in the door’s way. It controls the safety 5W2P valve and diverting valves.

Basic Information: The light curtain has two outputs but neither are compatible with the CNC. These outputs are called OSSD1 and OSSD2. These outputs are self checking; the worry is that the outputs will not be able to switch and the system will not be able to control the auto door. They test this by randomly switching the outputs. They switch for a very small amount of time (100s of microseconds). If they can switch, then everything is okay. If they cannot, then the light curtain detects this and forces the door open. This is the self checking process.

As stated earlier the light curtain’s outputs cannot be directly connected to the CNC. They must be connected to a safety relay. A safety relay takes both of the OSSD outputs, monitors them, and transforms them into one single output that can be read by the CNC. The safety relay also has self checking capabilities, identical to the light curtain’s.

The light curtain has a protective length of 6.3 inches.

Operation: The light curtain produces lasers between its two components. When an object gets in the way, both OSSD outputs will drop from 24V to 0V, attaching to the safety relay. The safety relay will then process this and close its output relay. 24V will then be sent to a relay in the back of the machine and will trigger the safety 5W2P valve and diverting valves. Specifically:

1 (Facing with label up), the left solenoid of the safety 5W2P will be actuated and held, (latched).

2 The diverting valves will actuate and be held, (latched), blocking Port 3 and allowing air to flow between Port 2 and Port 1. This will completely cut off the normal 5W2P valve.

3 This will force the door to open, (piston to extend).

4 The ladder code will time out and set an alarm, stopping the machine from operating.

5 When danger is concluded, the operator can press the ALARM RESET EMG. RELEASE button on the keyboard to shut off the safety system, deactivating the safety 5W2P valve, deactivating the diverting valves, (which allows the normal 5W2P to take control again), and normal operation will resume.

6 Keep in mind, the second the object is removed from the light curtain’s laser, the light curtain and safety relay will reset. At this point, only the machine is keeping the door open and the safety system engaged. This is adjustable, (see the Finishing Up the Lynx 220L (https://docs.google.com/document/u/0/d/1lHe_dQuX5BtElMpw_9GBA3AOfG6Tnj45F4rXxdiytM4/edit) document REF20).

Maintenance:

a) Double check metal debris is not resting on the piston. The debris will undoubtedly destroy the seal and render the air cylinder useless.
b) Squeaking usually means friction. Friction means wear. Make sure to lubricate any parts squeaking.
c) Periodically clean the light curtain’s sensors because dirt build up can hinder its ability to detect.
d) Clean debris from the door track.
e) If you want to go above and beyond, usually the manufacturers’ websites will have dedicated maintenance manuals for parts.

Adjust Door Speed:

There are multiple ways to adjust the door speed. Try to only adjust the speed using the flow control valves, not the overall system pressure. Remember, more pressure does not necessarily mean more airflow.

1 There are two sets of flow control valves: intake and exhaust. Examine Figure _, the left is the intake and the right is the exhaust.

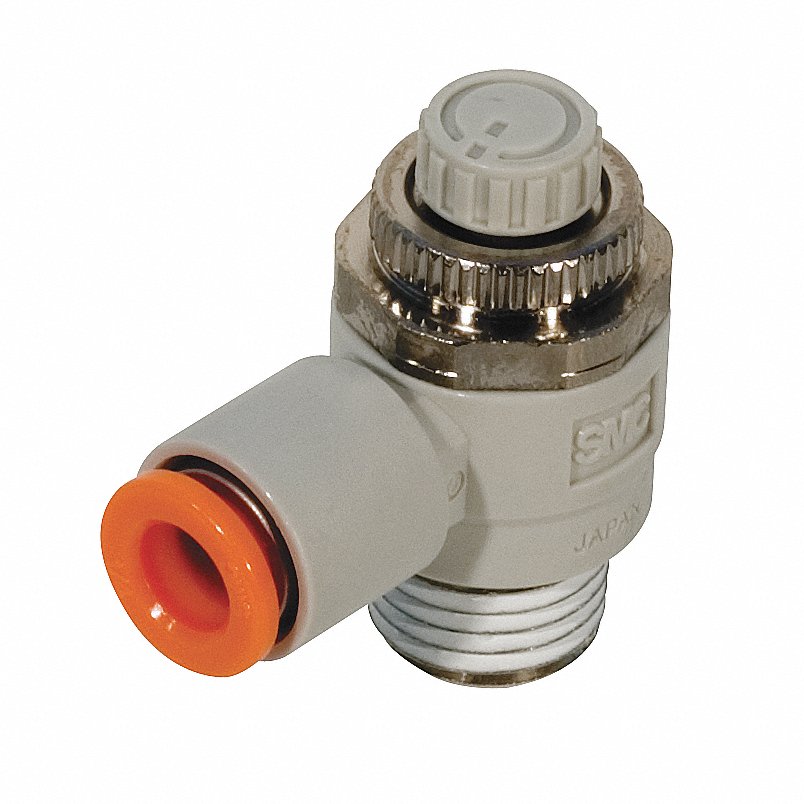
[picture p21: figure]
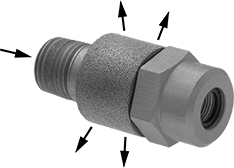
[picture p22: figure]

Figure :

The intake flow control valves are mounted directly on top of the air cylinder, there are two of them. The exhaust control valves are mounted to both 5W2P valves, there are four of them. To change speed follow the tables below:

Rotation (Exhaust Flow Control Valve) | Speed up or slow down?
Clockwise | Speed up
Counter clockwise | Slow down

Rotation (Intake Flow Control Valve) | Speed up or slow down?
Clockwise
Counter clockwise

2 To a certain extent, increasing the pressure will increase the door’s speed. Keep in mind increasing the pressure also increases the force the door will move with; the higher the force, the more wear on everything. Increasing the pressure will also change the behavior of the entire system. Only operate the system in the range of 12PSI to 96PSI, otherwise sluggish or bouncy behavior may occur.

The Power Cabinet (What Relays Used):

The power cabinet contains all electrical systems, (with the exception of the computers and circuitboards). This includes the relays used to operate the auto door as well as the 220V equipment. The 24V system will give you a nasty shock but likely will not do serious damage. The 220V system may hospitalize you. All of the 220V equipment is marked with a yellow sticker.

The power cabinet is located at the back of the machine. In the case of the Lynx 220, to access the power cabinet first loosen the two Allen bolts and twist the I/O knob all the way counterclockwise to release the door.

If the Fanuc I is off then the relays will also be off.

1L+ is 24V and 1M is 0V or common (and sometimes ground).

The relays work a little differently than how a stereotypical relay would work. Usually a relay is unpowered and acts only as a switch. The output relays (dictated by TM2) provide their own power so there is no need to wire it to a power terminal (1L+).

Table _ contains the parts and their relays. Keep in mind 1L+ is 24V source, M is ground. (If this table is difficult to understand you may need to look through the electrical manual for the power cabinet schematics as well as the How to Read the Code section on Page .)

Part | Relay Rack | Relay Name | Contact Name (for code)
Supply Solenoid | XT1105 (TM1) | Any 1L+ and M | None, no code needed
Normal 5W2P Valve | XT1104 (TM2) | Y1.1 Y1.2 | DOP.R DOC.R
Safety 5W2P Valve | XT1106 (TM2) | Y4.2 | M92.R
Diverting Valves | XT1106 (TM2) | Y4.2 | SDOP.R
Light Curtain/Safety Relay | XT1105 (TM1) | X12.4 | EDGE.M
Magnetic Proximity Sensor | XT1107 (TM1) | X10.4 | DOC.M (SX231)

How to Read the Code (Ladder Code):

There are simulators online that allow you to write some code and test it. This will aid you greatly in your learning but will also allow you to test your code before writing it to the CNC.

Part 1: Contacts

The CNCs, (the Lynx at least), allow you to watch the code while the machine operates. This can be very handy for troubleshooting. Likely the code itself will not fail, but because you can monitor the code in real time, it can show you which parts are not triggering. This is an alternative to pulling the parts and wires out and testing everything with a multimeter.

Observe Figure _. The symbol on the left represents a normally open contact and the right represents a normally closed contact.

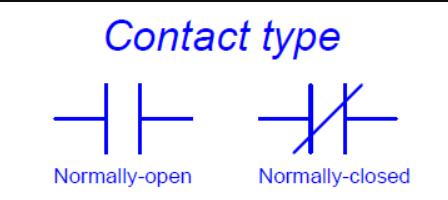
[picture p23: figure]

Figure :

The normally closed contact can be remembered because it has a slanted line between the vertical, representing a closed circuit, (a closed circuit will allow electricity to flow while an open circuit will not. Think of a light switch). The normally open contact has no slanted line and represents an open circuit, a circuit where no electricity flows. Here is a concise version:

Normally open = open circuit = no electricity

Normally closed = closed circuit = electricity

This is where it becomes more complicated. Each contact has two states: normal and actuated. Look at Figure _.

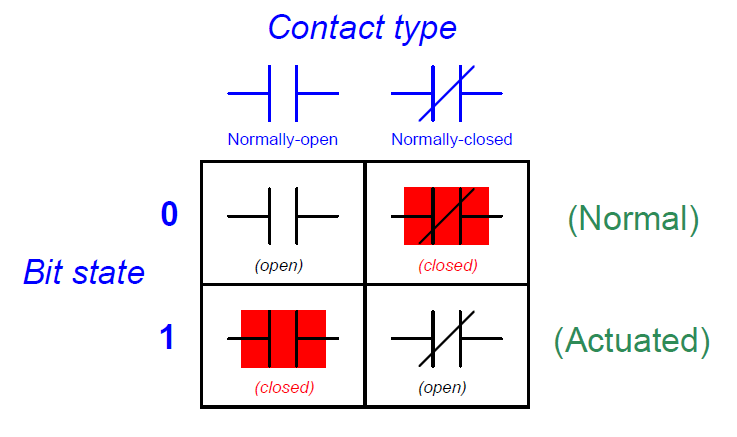
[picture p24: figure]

Let us examine the normally open contact first. The normally open contact has no electricity when it is in its normal state. But, just like a light switch, when it is flipped (actuated) it allows electricity to flow through it. The CNCs highlight the contact in color (usually blue but in this diagram it just happens to be red) to show electricity flowing through it.

The normally closed contact is the exact opposite of the normally open. In its normal state electricity is flowing, (shown by the red), and when it is flipped, (actuated), no electricity flows through it.

Okay so what exactly are contacts? This will be explained better in Part 3 but all contacts are just switches. There are three types: input relays, bits, output relays. But at the end of the day they are all just switches.

Part 2.1 Logic:

So what is the point of any of this? By chaining two contacts together we can give the computer “intelligence.” First let us look at AND logic. Look at Figure _. Here we have four circuits. Each one has two switches (treats these as the contacts we learned in Part 1) and one light bulb. Notice that only in the last circuit is the light bulb on. This is also the only circuit where both switches are closed. Let us compare.

In the first circuit, Switch B is ready to turn on the bulb but Switch A is not. In the second circuit, Switch A is now ready but Switch B is not. In the third, circuit neither switch is ready. In all three of these circuits because both switches are not ready the bulb never comes on. Even if one switch is ready, the other one has to be as well. This creates AND logic. You need Switch A AND Switch B.

So for example, we want the auto door to open if the chuck is completely stopped AND the coolant is off. This AND logic allows us to give the computer “intelligence.”

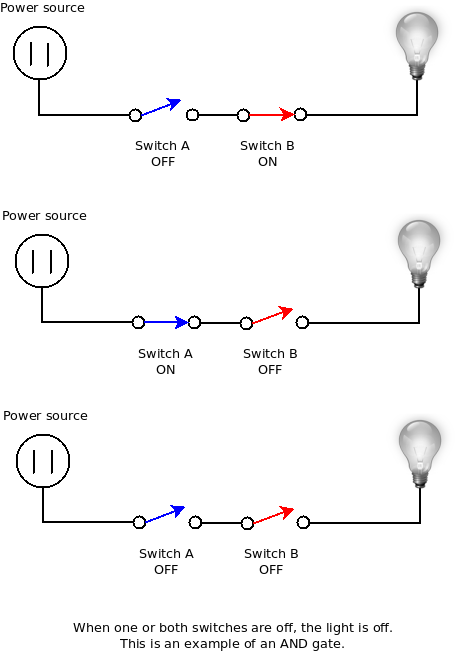
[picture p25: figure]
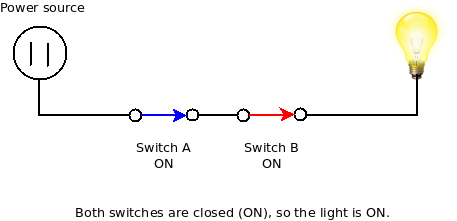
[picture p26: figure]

Figure :

Second, let us look at OR logic. Examine Figure _. Here we have four circuits. Each one has two switches (treats these as the contacts we learned in Part 1) and one light bulb. Notice that only in the third circuit is the light bulb off. This is also the only circuit where both switches are open. Let us compare.

In the first circuit, Switch A is not ready but Switch B is; this means the bulb is on. In the second circuit, Switch A is ready but Switch B is not; this means the bulb is on. In the third circuit, neither Switch A nor Switch B are ready; this means the bulb is off. In the fourth circuit, both Switch A and Switch B are ready; this means the bulb is on. In these circuits only one of the switches need to be ready for the bulb to turn on. This creates OR logic. Either Switch A or Switch, (or both), B can be ready for the bulb to be on.

So for example, we want the auto door to close if the safety curtain is tripped OR the operator closes it. This OR logic allows us to give the computer “intelligence.”

Part 2.2: Logic in Ladder Code

Take some time and become comfortable with AND and OR logic before moving on.

So how do we apply this to ladder code? The AND logic about the chuck being stopped and Coolant Off is shown in Figure _. A good way to think about ladder code is to think of it like electricity flowing from the left side to the right side. So in this case if both Chuck Stopped and Coolant Off are closed, (actuated), then electricity will flow through them and into the circle labeled Door Open. Figure _ is an example where the coolant is off but the chuck has not stopped and therefore the door is not open. (Remember, the pieces will be colored when electricity flows through it).

Figure _:

Figure _:

What is the circle? The circle represents a physical relay on the CNC, (an output relay). So in the ladder code we are “sending electricity from the left side to the right side,” that is basically what we are doing in real life as well. In this case, (but not always), Chuck Stopped and Coolant Off are relays too, input relays. In real life, they would likely be plugged into a sensor. So, yet again, electricity is flowing from the sensors “through the code” and into the output relay Door Open.

As a side note, you may be wondering why normally open contacts were chosen for the Chuck Stopped and Coolant Off. It is based on the sensor type. Sensors can either supply 24V when triggered, (they will be called Electricity When Triggered), or can drop to 0V when triggered, (they will be called No Electricity When Triggered). Why would that even exist?

The Electricity When Triggered Sensor is “normal.” When nothing is happening, then there is no voltage. This is intuitive to people because it is essentially saying, “When nothing is happening, voltage off. When something is happening, voltage on.”

The No Electricity When Triggered Sensor is used in safety for power outages. This is how a light curtain works. When everything is fine it produces 24V. When someone puts their hand in the way, it drops to 0V. If the power goes out, well, the voltage goes to 0V and the safety state is triggered.

This all seems unnecessarily complicated but it actually can simplify things. What if

Also, Electricity When Triggered = normally open. No Electricity When Triggered = normally closed. Pretty much everything in ladder code is just understanding normally closed and normally open.

Part 2.3 Combining OR and AND logic

Okay so now let us combine AND and OR logic. Look at Figure _. As we can see we have our familiar AND logic with Chuck Stopped and Coolant Off. But now we have a different branch, (they are actually called rungs), that has the Master Override contact in it. If we again think of electricity flowing from the left to the right we can see that if Master Override is triggered, then so is Door Open even if Chuck Stopped and/or Coolant Off is not. This is our OR logic.

So AND logic is represented by two or more contacts in series. OR logic is represented by two or more contacts in parallel.

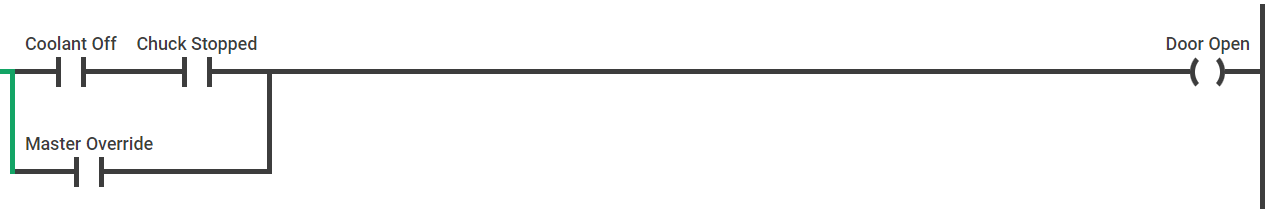
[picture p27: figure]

Figure :

Part 2.4 How the Computer Reads Ladder Code:

How does the computer know what to read and when? The computer will read the code left to right, up to down. In this case Chuck Stopped will always be read first because it is the most left on the top rung. Then Coolant Off will be read. Then it would look at Door Open and see if it has electricity to it. Next Master Override will be read and, again, it would look at Door Open to see if there is electricity to it. Then the computer would skip to the next rung dealing with some other part of the machine. The computer will read the code similarly to how you would read a book, start at the top, read left to right.

To be more specific, the computer does three scans:

1 Check the state of the inputs, on or off

2 Check to see if any of them have changed

3 Change the outputs accordingly

The computer will read all of this code very, very quickly, (usually within a couple hundred microseconds). This causes a problem. If you wanted to hit the Master Override button, by the time it took you to press and release the button, the computer has read the code probably 10 times. Honestly it is kind of a questionable design and it stumped me for a while. This is why latching becomes important; latching will be covered in Part 2.5.

One final note. We have already discussed input and output relays but there is a third type of contact: bits. Bits are also switches but they are internal to the computer, (they are transistors). Bits have no way to interact with the “real” world, aka, they are not input or output relays. Bits can be used in lots of different ways; the good news is that most of these ways revolve around the same idea: to make connections between relays without having to directly wire them together. An example is given in Figure _.

Figure _:

Let us say ARST is a contact for the reset button that is actually on the machine’s keyboard, (technically ARST is not but for this example let us just say that). INRST is a bit and is designed to be a reset system for the door specifically. We can see this because DOP.R is used with it.

Even though INRST and ARST are essentially doing the same thing, INRST is an “upgraded” version of ARST; it includes more about the door. By using bits we can either enhance the ability of a button/relay or design a button/relay specifically for a situation. None of this is very clear unfortunately but it comes with practice.

One final note about bits. How do we know when a contact is a bit? When you select a contact, (in edit mode), it will give you the technical name of the contact. If it has a X in front of it (like X13.7) then it is an input relay. If it has a Y in front of it (Y3.3) then it is an output relay. If it has neither then it is a bit.

Part 2.5 Latching:

Let us start with a problem first. Let us say we want to install a light inside the chamber that is controlled by a button on the machine. We want the light to stay on after we pressed the button; with our understanding of ladder code right now that would not be possible. The second the operator releases the button, the contact would be released as well and the light would turn off. So how do we keep the light on?

We achieve this by latching. Latching is exactly what it sounds like; it latches the contact either open or closed. Observe Figure _ and Figure _ which is our first attempt at latching.

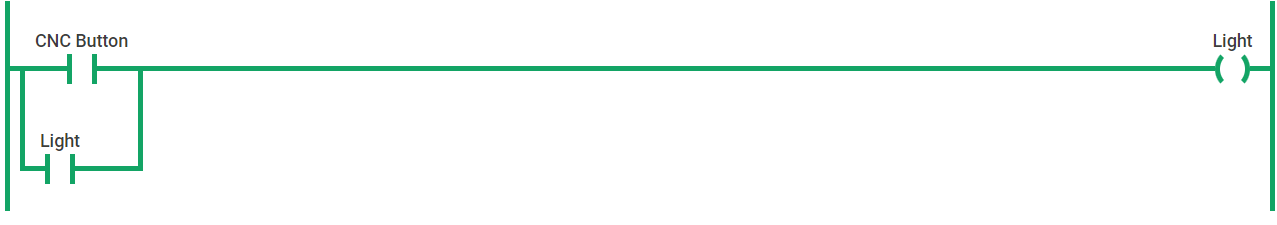
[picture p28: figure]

Figure _:

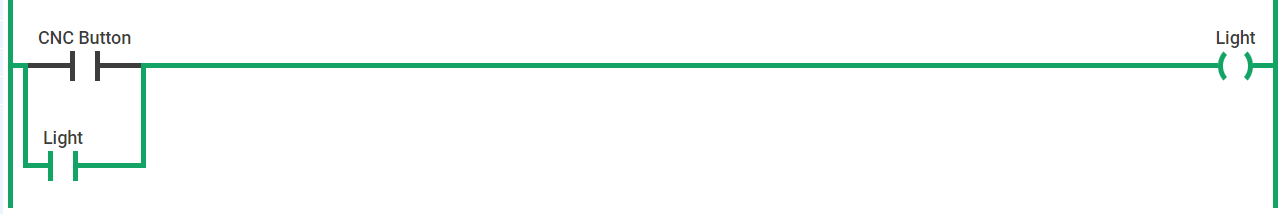
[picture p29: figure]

Figure _:

Notice how Light is an input and an output. This may seem strange at first but remember the goal; if Light is on we want it to stay on. As seen in Figure _ and Figure _, no matter if CNC Button is on or off, Light stays on.

Great, so the light inside the machine stays on and we are done? No. How do we turn off the light?

We need to add a reset contact, one that is normally closed. Observe Figure _.

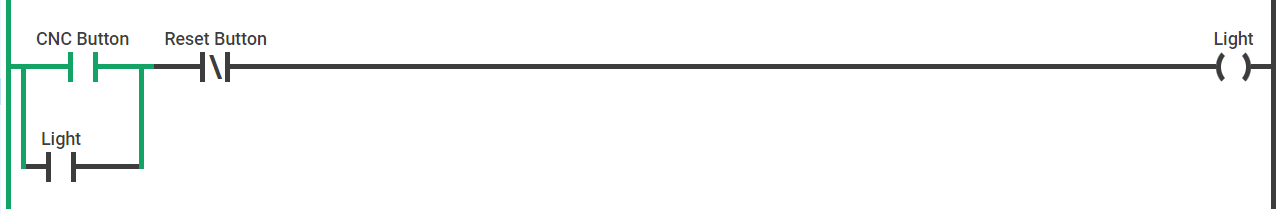
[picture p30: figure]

Figure _:

Now the operator is able to turn off the light by using the Reset Button. (Performing the simulation of this makes it much clearer). Obviously having two separate buttons, (Light Button and Reset Button), to operate one light is kind of inconvenient. But this is just to demonstrate the idea of latching. The actual code for latching and unlatching for a single button, (called toggling), is more complicated and can be found online by searching “how to toggle in ladder code.”

Part 3 The Actual Code:

This is going to be kind of a jump in difficulty but we needed to discuss the actual code eventually. Look at Figure _, which is the actual code used in the CNC. (The states of the contacts in Figure _ are not relevant to what is written here. Pay attention only to the structure and order of the contacts, not which ones happen to be actuated in this photo).

All of these rungs lead to a contact named DOP.R which is an output relay to open the door. (In terms of our actual system, this relay will actuate and electricity will then flow to the normal 5W2P valve). We know it is a relay because it has .R in its name. We can also look at the electrical manual to see all of the inputs and outputs.

Look at the second rung. The first contact is M52, and since this is a M-Code command, it is a bit contact, (has no real relay). The second contact is DOC.M which is an input relay, (from the manual). DOC.M connects to the magnetic proximity sensor that “tells” the CNC when the auto door is finally open. Finally we have SSTA which is a bit contact as well which tells us if the chuck has stopped spinning. (You may think this is an input because it comes from some sensor measuring the chuck speed right? Well, yes, but this sensor input is processed through a circuitboard and then the computer sends the signal internally. This does not have to be the case but that is the way the engineers made it. It could have easily been a sensor that plugs into the input relays instead of a circuitboard. Confusing I know.)

All three of these have been ANDed with each other. Remember that the contacts in blue means electricity is flowing through them. So we need three things to happen before the door opens:

1 M52 is normally open which means it needs to be actuated for electricity to flow through it. This is achieved by writing M52 in the M-Code.

2 DOC.M is normally closed which means we do not want it to be actuated for electricity to flow.

3 SSTA is normally open which means it needs to be actuated for electricity to flow through it. In this case the chuck stops and the circuitboard triggers the contact.

But there is actually one more contact we have to consider even though it is not unique to this rung: TMB129. This is a special contact called a timer. It behaves exactly like a timer. In this case when it is triggered it counts up, causing a delay. We want this delay because we want the door’s interlock to release before the air cylinder tries to open the door.

Let us examine the last rung with a contact called CLINT. CLINT stands for CLose door INTerrupt. This is our safety system. Notice how it is not ANDed with anything at all. Why? Because we always want the safety system to take control.

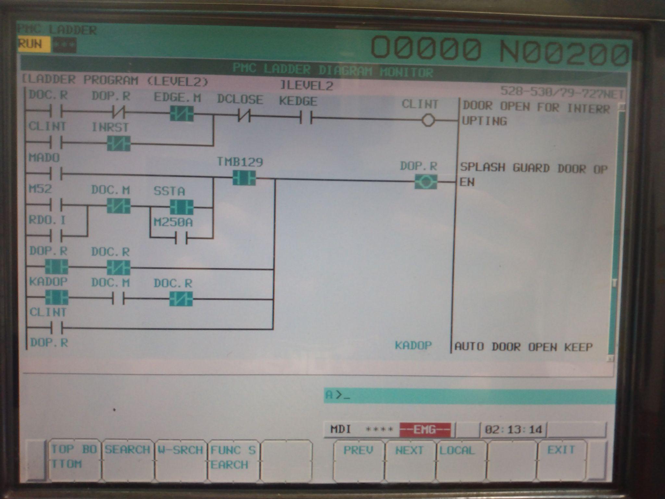
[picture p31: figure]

Figure :

Troubleshooting:

BE SURE THAT NO ONE IS NEAR THE DOOR NOR ELECTRICAL SYSTEM WHEN TROUBLESHOOTING. YOUR ACTIONS COULD CAUSE THE DOOR TO MOVE WITHOUT POSSIBILITY OF BEING STOPPED. TURN OFF THE AIR SUPPLY IF IT IS NOT NECESSARY FOR THE TROUBLESHOOTING AND EVACUATE BOTH CHAMBERS OF THE AIR CYLINDER BY DISCONNECTING THE LINES TO IT, STARTING WITH THE HOSE AT THE BACK OF THE CYLINDER.

Try the Quick System Check First:

Door Does Not Open:

1 Is the safety system on?

a) Press the MESSAGE button on the keyboard. Does it say “NO. 2040 SPLASH GUARD, DOOR OPENED / OPERATOR’S DOOR OPENED”? Press the ALARM RESET EMG. RELEASE button on the keyboard to fix it.

2 Check the fuses for the 5W2P valves.

a) Power down the machine and turn off the circuit breaker. Wait 20-30 minutes.
b) Find the normal 5W2P valve. The fuse holder should be attached to the red wire.
c) Remove the top of the fuse holder and pull the fuse out
d) Grab a multimeter and find the continuity setting. First, touch the red connector and the black connector together to test the buzzer inside the multimeter; if it beeps then you are good, if not then you need to replace the multimeter. Next, place the red connector on one leg of the fuse and the black connector on the other leg of the fuse. If you hear the multimeter beep, then the fuse is good. If it is silent, the fuse is blown and needs to be replaced. It is a 2 amp automotive fuse you can grab from O'Reillys or Autozone.
e) Once the new fuse is obtained place it firmly into the fuse holder, (it does not matter which way you insert it), snap the lid back on firmly, and power the CNC back on, TAKING CARE TO MAKE SURE NO ONE OR NOTHING IS IN THE DOOR’S WAY.

2 Test the normal 5W2P valve’s solenoids with the 24V Tester.

Tools Needed:

24V Tester
Extension Cord

Alligator Clips (Optional)

Multimeter

a) Power down the machine and turn off the circuit breaker. Wait 20-30 minutes.
b) While waiting, set up the extension cord and 24V Tester. We will test the 24V Tester to make sure it is working. Separate the red and black wires. Set the multimeter setting to 200V. Connector the red lead of the multimeter to the red wire of the 24V Tester. Do the same with the black wires. Plug in the 24V Tester. The multimeter should read about 24V, (1 or 2 volts over or under is okay, you’re looking for something far from 24V). (Also -24V is okay as well).
c) Find the normal 5W2P valve. With the label visible, remove the screw on the top of the left DIN connector with a flathead screwdriver.
d) Remove the DIN connector placing it somewhere with no metal.
e) Connect the red and black wires of the 24V Tester as shown in Figure _.
f) Double check the wires are not touching each other before plugging the 24V Tester into the extension cord. Hold the solenoid with a hand. Plug the 24V Tester in. A click should be heard/felt.

A) It might be loose connections on the solenoid’s leads. Turn off the CNC and remove any power source to it, (flip off the breaker labeled Lynx). Wait the recommended time for the internal circuitry to discharge, (found in the CNC machine’s maintenance manual). Inspect the connections to see if they are loose, burn, or stripped(lots of the strands of copper wire are missing).

B) The wires themselves might be damaged. Turn off the CNC and remove any power source to it, (likely just the plug in the wall). Wait the recommended time for the internal circuitry to discharge, (found in the CNC machine’s maintenance manual). Turn on the multimeter and find the continuity setting. First, touch the red connector and the black connector together to test the buzzer inside the multimeter; if it beeps then you are good, if not then you need to replace the multimeter. Place one connector at one end of the wire and the other connector at the other end. If the multimeter beeps then the wire is not broken, if no beeping then replace the wire.

Door does not close:

1 Check the fuses for the 5W2P valves.

First power down the CNC and lock it out if you feel the need. If the door does not open during normal operation, check the fuses on the normal 5W2P valve. If the door does not open during safety state, check the fuses on the safety 5W2P valve. The fuses have a container in which you can remove the top. If the fuse is blown you can usually just see that it is disconnected. If you want to be extra sure, grab a multimeter and find the continuity setting. First, touch the red connector and the black connector together to test the buzzer inside the multimeter; if it beeps then you are good, if not then you need to replace the multimeter. Next, place the red connector on one leg of the fuse and the black connector on the other leg of the fuse. If you hear the multimeter beep, then the fuse is good. If it is silent, the fuse is blown and needs to be replaced. It is a 2 amp automotive fuse you can grab from O'Reilly’s or Autozone.

Once the new fuse is obtained place it firmly into the fuse holder, (it does not matter which way you insert it), snap the lid back on, and power the CNC back on, TAKING CARE TO MAKE SURE NO ONE OR NOTHING IS IN THE DOOR’S WAY.

2 Test the normal 5W2P valve’s solenoids with a multimeter.

Figure _ shows which side closes the door. Start with removing the DIN connector, (the submarine scope looking piece), by removing the screw on the top. THERE ARE LIVE CONNECTIONS UNDERNEATH THE DIN CONNECTOR SO BE CAREFUL. Slide the DIN connector far enough off the metal leads until you see three prongs. Switch your multimeter to voltage (in V, not mV), and place the red connector and black connector as shown in Figure _. It should read about 24V (1 or 2 volts over or under is okay, you’re looking for something far from 24V). It can either be positive or negative 24V, it does not matter in this case.

If you are not receiving any voltage:

A) It might be loose connections on the solenoid’s leads. Turn off the CNC and remove any power source to it, (likely just the plug in the wall). Wait the recommended time for the internal circuitry to discharge, (found in the CNC machine’s maintenance manual). Inspect the connections to see if they are loose, burn, or stripped(lots of the strands of copper wire are missing).

B) The wires themselves might be damaged. Turn off the CNC and remove any power source to it, (likely just the plug in the wall). Wait the recommended time for the internal circuitry to discharge, (found in the CNC machine’s maintenance manual). Turn the multimeter and find the continuity setting. First, touch the red connector and the black connector together to test the buzzer inside the multimeter; if it beeps then you are good, if not then you need to replace the multimeter. Place one connector at one end of the wire and the other connector at the other end. If the multimeter beeps then the wire is not broken, if no beeping then replace the wire.

C) Possibly the 5W2P valve’s solenoid is damaged. Turn off the CNC and remove any power source to it, (likely just the plug in the wall). Wait the recommended time for the internal circuitry to discharge, (found in the CNC machine’s maintenance manual). Turn off the main air supply. Remove the the wires from the solenoid leads and find a 24V power source, (like one you plug into a wall for example), and connect the red and black wire to the leads shown above in Figure _. You should hear a somewhat quiet click. If not, the solenoid is definitely broken. If you do, this does not necessarily mean everything is okay.

3 The magnetic proximity sensor

that tells the CNC when the door is fully open is not working or has been wiggled out of its operating distance. This will need to be tested with the power on. Be careful to not touch the metal parts of the wires.

A) First make sure the proximity sensor has not strayed from its mounting place. The proximity sensor is triggered when a magnet is near. This triggering is shown by a orangeish LED lighting up. The magnet on the air cylinder is right in front of the rear black endcap, (the magnet is connected to the back of the piston inside the casing so you will not be able to see it). Make sure the proximity sensor is mounted so that the orangish LED stays on.

B) If the proximity sensor does recognize the magnet, then test the output of the proximity sensor. The proximity sensor has three wires: brown, blue, and black. The brown wire is for 24V. The blue wire is for 0V, (or ground). Grab a multimeter and switch it to the V setting, (not mV). Place the red connector to the brown wire and the black connector to the blue wire. We want the multimeter to read 24V (1 or 2 volts above or below 24V is okay, you are looking for way less or more than 24V). If it is not receiving 24V then there is a loose connection or the wire is damaged. Turn off the CNC and remove any power source to it, (likely just the plug in the wall). Wait the recommended time for the internal circuitry to discharge, (found in the CNC machine’s maintenance manual). Turn the multimeter and find the continuity setting. First, touch the red connector and the black connector together to test the buzzer inside the multimeter; if it beeps then you are good, if not then you need to replace the multimeter. Place one connector at one end of the wire and the other connector at the other end. If the multimeter beeps then the wire is not broken, if no beeping then replace the wire.

Next, leave the black connector attached to the blue wire. Place the red connector on the black wire, (black wire of the sensor not the multimeter), When the proximity sensor is not near a magnet, (when the orangish LED is not on), this should read 0V. Bring the proximity sensor near enough to a magnet so that the orangeish LED comes on. The multimeter should read about 24V (1 or 2 volts above or below 24V is okay, you are looking for way less or more than 24V). If the voltage reading is not 0V away from the magnet and not 24V near the magnet then the sensor needs to be replaced.

Noisey Parts:

If the pneumatic parts start clacking or clanking it is usually due to abrupt or inconsistent airflow. Abrupt airflow can be fixed by:

1 Checking if any of the valves are damaged through visual inspection or disassembly

2 Adjusting operating pressure via regulator

3 Something in the system has changed and may require a soft start valve. This would be placed at the beginning of the pneumatic system, likely after the supply solenoid valve.

Inconsistent airflow can be fixed by:

1 Check that each valve can be fully actuated and is not blocked by debris.

2 Check for damaged valves

If the valves emit a rapid clicking it means the solenoid is not receiving enough electrical power to remain on. This should be stopped immediately as it damages the part. This can be fixed by:

1 Ensuring the part is receiving the power it needs. To do this, measure the voltage and current with a multimeter, multiply the two numbers, and see if it is close to the watts given on the part’s sticker.

2 Inspect the solenoid for any damage or debris.

Light Curtain Does Not Open Door:

If the door is closed and the door interlock system is engaged, the light curtain cannot open the door. (It will still react to objects breaking the lasers’ paths though).

Door Time Out Alarm Message:

Quick System Check:

The following is a quick way to test all the components. This would be a good procedure to use every couple weeks to every month. It also can serve as a quick way to troubleshoot the system.

a) Grab another operator who knows how to use MDI
b) One person will place their hand on the valves to test, (call them Outputter), and one will enter code from the keyboard, (Inputter).
c) Outputter: Locate the normal 5W2P valve. With the valve orientated so the label is visible, place hand on on the left solenoid

Inputter: Open the door with M52; in MDI

Outputter: A click should be felt/heard

d) Outputter: Stay with the normal 5W2P, place hand on right solenoid

Inputter: Close the door with M53; in MDI

Outputter: A click should be felt/heard

e) Outputter: Find the safety 5W2P, (one set of wire from the DIN connector), as well as the diverting valves. With the valve oriented so the label is visible, place one hand on the left solenoid. Place the other hand on both diverting valves.

Inputter: Ensure the door is fully open. Trigger the light curtain by inserting an object, (not an arm or hand), into the path of the light curtain.

Outputter: A click should be felt/heard

Inputter: Press ALARM RESET EMG. RELEASE button on the keyboard

Outputter: A click should be felt/heard

f) If part e is inconclusive, do the following:

Inputter: Be sure the safety system is triggered by observing that the splash guard door alarm is set by pressing the Message button on the keyboard. (Additional check: attempt to close the door with M53;. If it does not close and the alarm is still on, continue. If it closes will the alarm is still on, there is a bigger problem)

Outputter: Locate the pressure regulator. Turn down the pressure to 20PSI or lower. Return to the normal 5W2P valve. Disconnect air hoses from Port 2 and Port 4, (air should be emitted that is okay). Locate the air cylinder. Disconnect air hoses from both ports. If air is emitting from these hoses then the safety system is not functioning. DO NOT OPERATE THE MACHINE. If there is no air then continue to Part g.

g) Outputter: Locate the supply valve. Place one hand on the solenoid.

Inputter: Turn off the computer, (but not necessarily all the power).

Outputter: A click should be felt/heard

Inputter: Turn the computer back on

Outputter: A click should be felt/heard

h) (Do not stress about messing up the ladder code. It is a very specific and multistep process to modify the ladder code. That being said, if you ever see a button that is named EDIT, stop immediately and refer to the Someone Left Edit Mode On section).

h.1) Close the auto door using the M53; with MDI
h.2) Press the SYSTEM button on the keyboard, top right

h.3) Press the right arrow button right below the screen until PMC LADDER appears on the screen

h.4) Press the blank button right under where it says PMC LADDER

h.5) Press the blank button under LADDER

h.6) Press the blank button under (OPRT)

h.7) Press the blank button under SEARCH MENU

h.8) Type in DOC.M

h.9) Press the blank button under SEARCH

h.10) Press the blank button under NEXT until the layout shown in Figure _ is found.

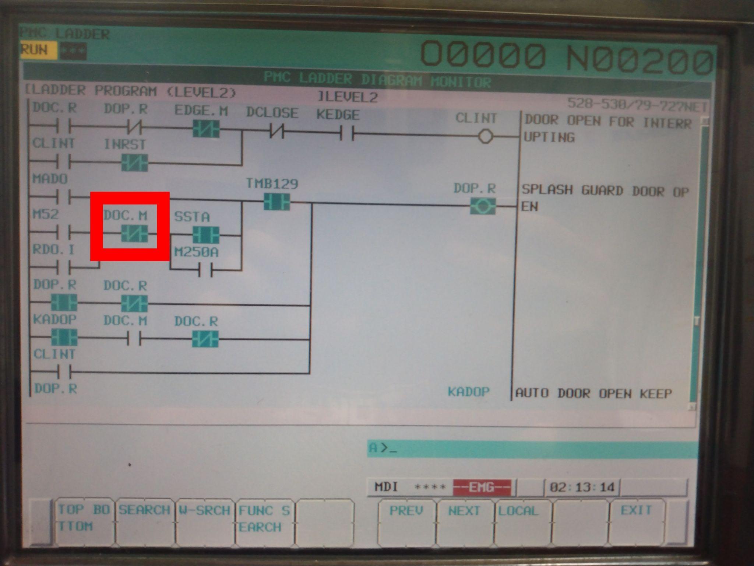
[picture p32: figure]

Figure _:

h.11) DOC.M, (focus on the one highlighted in the red box in Figure _), should be colored blue.

h.12) Press the PROG button

h.13) Open the door by typing in M52; in MDI

h.14) Press the SYSTEM button on the keyboard, top right

h.15) Press the right arrow button right below the screen until PMC LADDER appears on the screen

h.16) Press the blank button right under where it says PMC LADDER

h.17) Press the blank button under LADDER

h.18) Press the blank button under (OPRT)

h.19) Press the blank button under SEARCH MENU

h.20) Type in DOC.M

h.21) Press the blank button under SEARCH

h.22) Press the blank button under NEXT until the layout shown in Figure _ is found.

h.23) DOC.M should no longer be blue

i) Two notes before Step i is executed. Note 1: This is Lynx 220L specific; if following this process with another machine, be aware that some steps may be different.

Note 2: Step i requires opening the power cabinet while the power is on. Be careful to not touch ANYTHING other than the power cabinet doors, the power switch, and the release lever for the power switch

i.1) Turn off the Lynx 220L

i.2) Open the power cabinet doors

i.3) Hold the power switch release lever still and rotate the knob to the on position

i.4) Have a second person turn on the computer

i.5) The safety relay should have three green LEDs on.

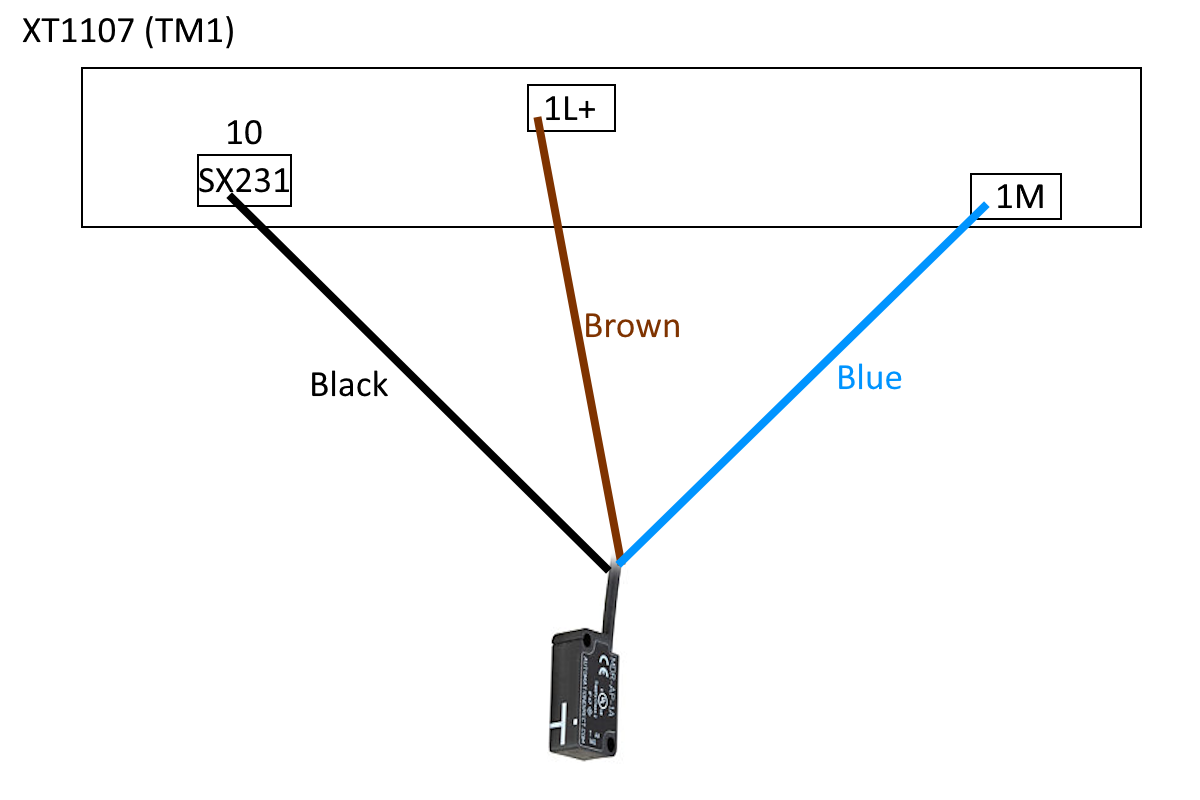
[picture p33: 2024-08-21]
Technician Diagrams/Magnetic Proximity Sensor Wiring Diagram.png

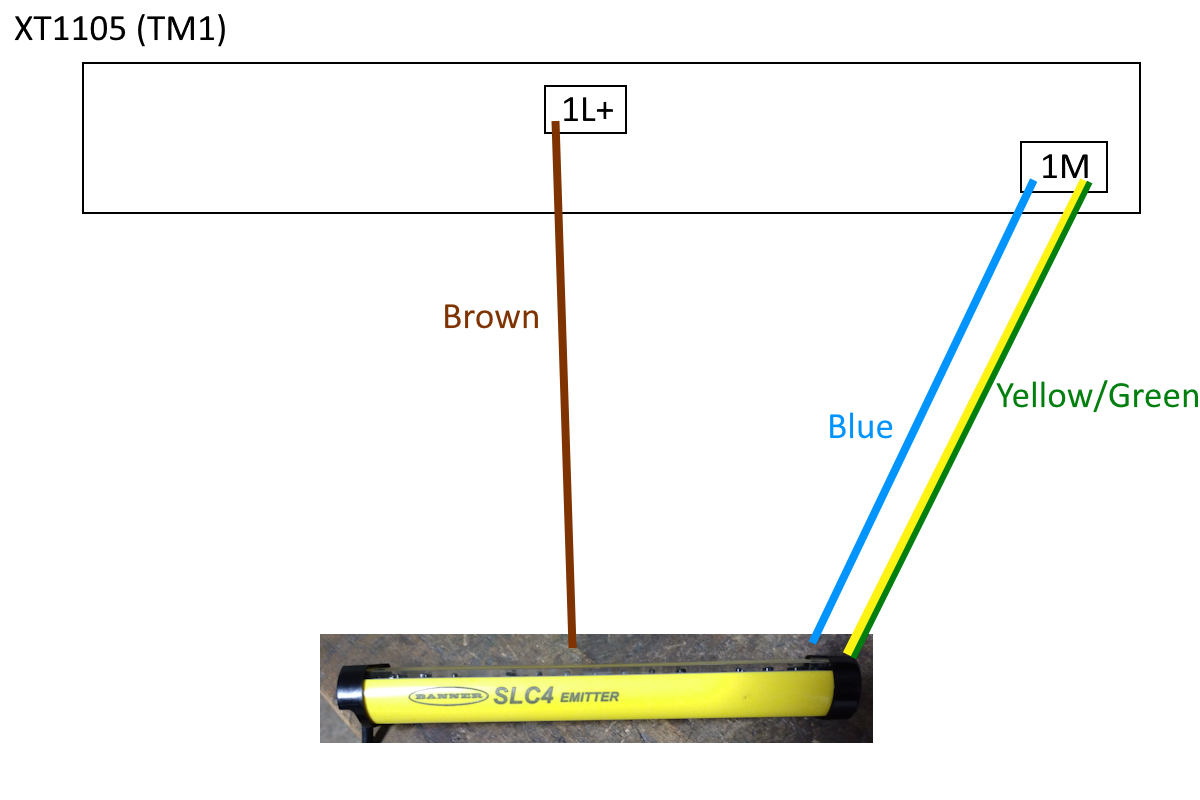
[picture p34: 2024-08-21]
Technician Diagrams/Light Curtain Emitter Wiring Diagram.png

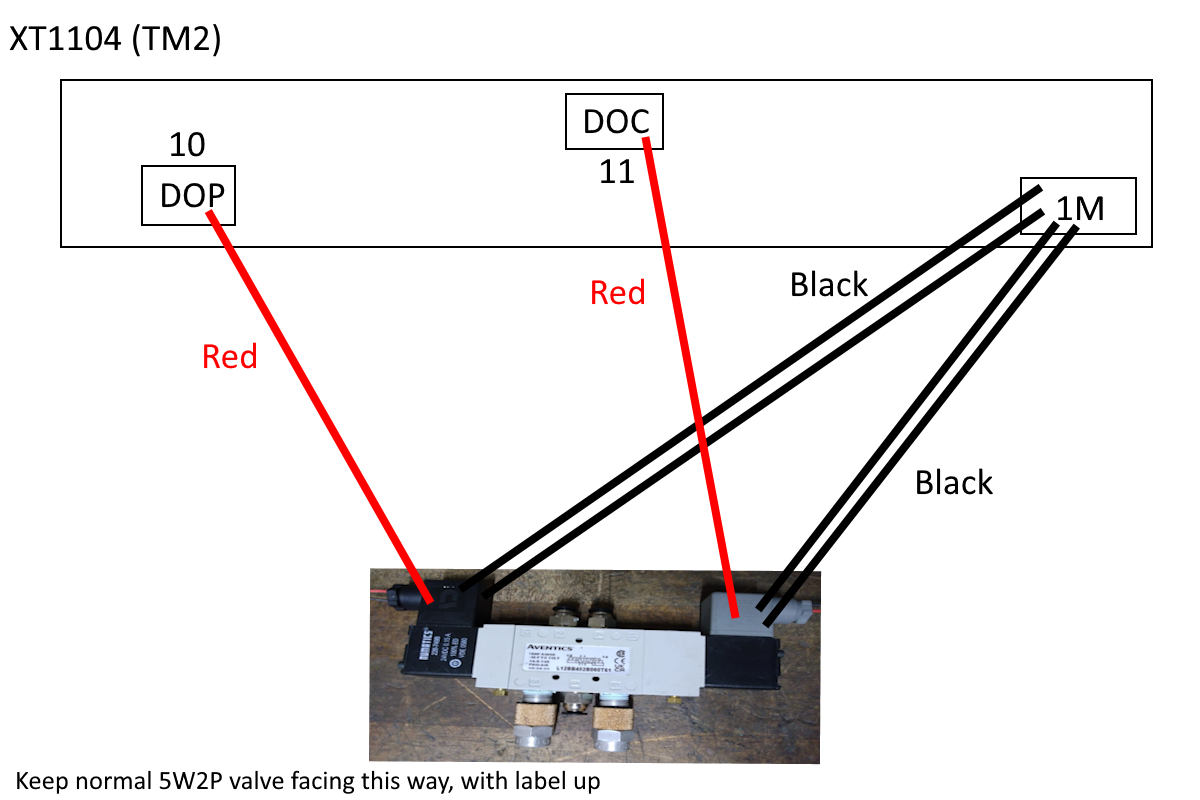
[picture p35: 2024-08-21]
Technician Diagrams/Normal 5W2P Valve Wiring Diagram.png

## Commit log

2024-08-21 Rename 3 Way Diverting (Switch) Valve Bracket.3MF to Technician Diagrams/3 Way Diverting (Switch) Valve Bracket.3MF
    [3 Way Diverting (Switch) Valve Bracket.3MF]
2024-08-21 Rename Air Cylinder Nose Bracket.SLDPRT to Technician Diagrams/Air Cylinder Nose Bracket.SLDPRT
    [Air Cylinder Nose Bracket.SLDPRT]
2024-08-21 Rename Conveyor Belt Retroreflector Bracket.SLDPRT to 3D Printer Files (Solidworks)/Conveyor Belt Retroreflector Bracket.SLDPRT
    [Conveyor Belt Retroreflector Bracket.SLDPRT]
2024-08-21 Rename Conveyor Belt Sensor Bracket.SLDPRT to 3D Printer Files (Solidworks)/Conveyor Belt Sensor Bracket.SLDPRT
    [Conveyor Belt Sensor Bracket.SLDPRT]
2024-08-21 Rename Light Curtain Emitter (Top) Bracket Washer 3mf.3MF to 3D Printer Files (Solidworks)/Light Curtain Emitter (Top) Bracket Washer 3mf.3MF
    [Light Curtain Emitter (Top) Bracket Washer 3mf.3MF]
2024-08-21 Rename Light Curtain Emitter (Top) Bracket Washer.SLDPRT to 3D Printer Files (Solidworks)/Light Curtain Emitter (Top) Bracket Washer.SLDPRT
    [Light Curtain Emitter (Top) Bracket Washer.SLDPRT]
2024-08-21 Rename Light Curtain Emitter (Top) Bracket.SLDPRT to 3D Printer Files (Solidworks)/Light Curtain Emitter (Top) Bracket.SLDPRT
    [Light Curtain Emitter (Top) Bracket.SLDPRT]
2024-08-21 Rename Light Curtain Receiver (Bottom) Bracket Resized 3mf.3MF to 3D Printer Files (Solidworks)/Light Curtain Receiver (Bottom) Bracket Resized 3mf.3MF
    [Light Curtain Receiver (Bottom) Bracket Resized 3mf.3MF]
2024-08-21 Rename Light Curtain Receiver (Bottom) Bracket Resized.SLDPRT to 3D Printer Files (Solidworks)/Light Curtain Receiver (Bottom) Bracket Resized.SLDPRT
    [Light Curtain Receiver (Bottom) Bracket Resized.SLDPRT]
2024-08-21 Rename Pressure Regulator Bracket.SLDPRT to 3D Printer Files (Solidworks)/Pressure Regulator Bracket.SLDPRT
    [Pressure Regulator Bracket.SLDPRT]
2024-08-21 Rename 3 Way Diverting (Switch) Valve Bracket.3MF to 3 Way Diverting (Switch) Valve Bracket
2024-08-21 Rename Air Cylinder Nose Bracket.SLDPRT to Air Cylinder Nose Bracket.SLDPRT
    [Air Cylinder Nose Bracket.SLDPRT]
2024-08-21 Rename Light Curtain Emitter Wiring Diagram.png to Technician Diagrams/Light Curtain Emitter Wiring Diagram.png
2024-08-21 Rename Light Curtain Receiver_Safety Relay Wiring Diagram.png to Technician Diagrams/Light Curtain Receiver_Safety Relay Wiring Diagram.png
2024-08-21 Rename Magnetic Proximity Sensor Wiring Diagram.png to Technician Diagrams/Magnetic Proximity Sensor Wiring Diagram.png
2024-08-21 Rename Normal 5W2P Valve Wiring Diagram.png to Technician Diagrams/Normal 5W2P Valve Wiring Diagram.png
2024-08-21 Rename Pneumatic System Layout Picture (Figure _).png to Technician Diagrams/Pneumatic System Layout Picture (Figure _).png
2024-08-21 Rename Safety 5W2P Valve_Diverting Valves Wiring Diagram.png to Technician Diagrams/Safety 5W2P Valve_Diverting Valves Wiring Diagram.png
2024-08-21 Rename Supply Valve Wiring Diagram.png to Technician Diagrams/Supply Valve Wiring Diagram.png
2024-08-21 Rename White Industries Projects Bill of Materials.xlsx to Documents/White Industries Projects Bill of Materials.xlsx
    [White Industries Projects Bill of Materials.xlsx]
